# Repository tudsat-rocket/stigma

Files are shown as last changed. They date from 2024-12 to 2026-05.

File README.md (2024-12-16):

# Stigma

the core- and mission board for our new flight computer

## Core Board
The core board will be placed on the mission board and will contain all basic and always-needed stuff. Powered by an STM32H7

## Mission Board
The mission board will contain all the other components but may change for future use cases of the core board.

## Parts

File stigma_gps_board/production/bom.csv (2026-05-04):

Designator | Footprint | Quantity | Value | LCSC Part #
C1, C2 | 0603 | 2 | 1uF | C15849
C3, C4, C5 | 0603 | 3 | 100n | C14663
J1 | DF40GB-70DP-0.4V-plug | 1 | DF40GB-70DP-0.4V | C2692097
L1 | 0603 | 1 | BEAD | C19330
L2 | 0603 | 1 | BEAD
TP1 | TestPoint_Pad_D1.5mm | 1 | tx
TP2 | TestPoint_Pad_D1.5mm | 1 | rx
TP3 | TestPoint_Pad_D1.5mm | 1 | 3v3
U1 | TSOP-5_1.65x3.05mm_P0.95mm | 1 | NCP115AMX120TCG | C603505

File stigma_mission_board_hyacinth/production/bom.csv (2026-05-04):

Designator | Footprint | Quantity | Value | LCSC Part #
BZ1 | MagneticBuzzer_CUI_CMT-8504-100-SMT | 1 | Buzzer | C781886
C10, C16, C18, C22, C23, C3, C8 | 0805 | 7 | 22u | C45783
C11, C14, C25, C26, C27, C28, C29, C30, C35, C36, C37, C38, C39, C40, C44, C45, C49, C57 | 0402 | 18 | 100n | C1525
C15, C17, C21, C34, C4, C43, C48, C7, C9 | 0603 | 9 | 10u | C96446
C19, C20, C41, C5 | 0402 | 4 | 1u | C52923
C24, C6 | 0603 | 2 | 10u
C42 | 0402 | 1 | 470p | C1537
C50, C51 | 0402 | 2 | 10p | C32949
C52, C54 | 0402 | 2 | 100n
C53 | 0402 | 1 | 33n | C7419416
C55, C56 | 0603 | 2 | 22u | C45783
D10, D16, D17, D18, D19 | 0603 | 5 | white | C2290
D15, D2, D3 | D_SMA | 3 | SS34 | C8678
D5, D6, D8 | 0603 | 3 | red | C2286
F1 | 1206 | 1 | 3A | C99558
F2, F3, F4, F5 | 1206 | 4 | 10A | C207003
FB1 | 0603 | 1 | FerriteBead | C1002
J1, J2 | core-board-inner-mounting-holes | 2 | DF40C-70DS-0.4V(51) | C294854
J10, J9 | JST_GH_SM04B-GHS-TB_1x04-1MP_P1.25mm_Horizontal | 2 | JST-GH | C189895
J3, J4 | Molex_Micro-Fit_3.0_43045-0800_2x04_P3.00mm_Horizontal | 2 | ~
J5 | Molex_Micro-Fit_3.0_43045-1200_2x06_P3.00mm_Horizontal | 1 | ~
J6, J7 | SMA_Amphenol_132289_EdgeMount | 2 | SMA
J8 | RJ45_Wuerth_7499010211A_Horizontal | 1 | RJ45_Wuerth_7499010211A
JP3, JP4 | PinHeader_1x02_P1.27mm_Vertical | 2 | Jumper_2_Small_Open
JP5 | SolderJumper-2_P1.3mm_Bridged_Pad1.0x1.5mm | 1 | Jumper_2_Bridged
L1 | L_Wuerth_XHMI-6060 | 1 | 6u8
Q1 | DFN-8-1EP_3x3mm_P0.65mm_EP1.55x2.4mm | 1 | AON7423 | C99711
Q2, Q4 | SOT-23 | 2 | AO3400A | C20917
Q5, Q6, Q7, Q8 | DFN-8-1EP_3x3mm_P0.65mm_EP1.55x2.4mm | 4 | AON7544 | C315567
R1, R17 | 2512 | 2 | 5m, 1% | C723630
R10, R12, R15, R19, R25, R27, R28, R29, R37, R46, R48, R53, R55, R57, R59, R6, R60, R62, R64, R66, R7, R8, R9 | 0402 | 23 | 10k | C25744
R11, R26 | 0402 | 2 | 1k5 | C25867
R13, R14, R22, R44, R54, R58, R61, R65 | 0402 | 8 | 120 | C25079
R2, R3, R4, R56 | 0402 | 4 | 100k | C25741
R24, R34, R67 | 0603 | 3 | 0
R30, R31, R32, R33 | 0402 | 4 | 51 | C25125
R35, R36, R38, R41, R42, R43, R51, R52 | 0402 | 8 | 33 | C25161
R39, R50 | 0402 | 2 | 0 | C17168
R40 | 0402 | 1 | 12.1k | C25752
R45, R47 | 0603 | 2 | 270 | C22966
R68 | 0402 | 1 | 0
R69 | 0603 | 1 | 56k
R70 | 0603 | 1 | 10k
R72 | 0603 | 1 | 49.9
TP1, TP2, TP3, TP4, TP5, TP6, TP7 | TestPoint_Pad_D1.5mm | 7 | TestPoint
U10, U8 | SOIC-8_3.9x4.9mm_P1.27mm | 2 | MCP2562FD | C124016
U11, U13 | Ai-Thinker-Ra-01-LoRa | 2 | Ai-Thinker-Ra-01
U12 | SOT-563 | 1 | TPD4E1U06 | C527516
U14 | VQFN-24-1EP_4x4mm_P0.5mm_EP2.5x2.5mm_ThermalVias | 1 | LAN8742A | C621424
U15 | SOT-583-8 | 1 | TPS62933
U2, U3, U6, U7 | SOT-223-3_TabPin2 | 4 | AZ1117I-3.3 | C92102
U4 | SOT-23-6 | 1 | INA181A3 | C2652255
U9 | SOT-23-6 | 1 | INA181A2 | C2058784
Y1 | Crystal_SMD_3225-4Pin_3.2x2.5mm | 1 | 25MHz | C9006

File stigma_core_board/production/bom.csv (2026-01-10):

Designator | Footprint | Quantity | Value | LCSC Part #
C1 | 0603 | 1 | 4u7 | C19666
C10, C9 | 0402 | 2 | 2u2 | C12530
C11, C12, C13, C14 | 0402 | 4 | 10p | C32949
C15, C16, C17, C20, C21, C22, C24, C25, C27, C28, C29, C3, C30, C31, C34, C35, C36, C39, C4, C40, C5, C6, C7 | 0402 | 23 | 100n | C1525
C18, C23 | 0603 | 2 | 10u | C19702
C19 | 0603 | 1 | 22u | C86295
C2, C26, C33, C37, C8 | 0402 | 5 | 1u | C52923
C32, C38 | 0402 | 2 | 10n | C15195
D1 | 0603 | 1 | red | C2286
D2 | 0603 | 1 | yellow | C72038
D3 | 0603 | 1 | green | C965804
D4 | D_SOD-123 | 1 | ~ | C8598
FB1 | 0603 | 1 | FerriteBead_Small | C1002
J1 | Tag-Connect_TC2050-IDC-FP_2x05_P1.27mm_Vertical | 1 | TC2050
J3 | DF40GB-70DP-0.4V-plug | 1 | CONN PLUG 70POS SMD GOLD
J5 | USB_C_Receptacle_Palconn_UTC16-G | 1 | USB_C_Receptacle_USB2.0 | C709357
R1, R2, R3, R4 | 0402 | 4 | 0 | C17168
R10, R11 | 0402 | 2 | 5k1 | C25905
R12, R13, R16, R17, R18, R19, R20 | 0402 | 7 | 22 | C25092
R14 | 0402 | 1 | 4k7 | C25900
R15 | 0402 | 1 | 10k | C25744
R5 | 0402 | 1 | 100k | C25741
R6, R7, R8, R9 | 0402 | 4 | 1k | C11702
SW1, SW2 | SW_Push_1P1T_NO_CK_KMR2 | 2 | KMR721NGLFS | C2911418
U1 | LQFP-100_14x14mm_P0.5mm | 1 | STM32H743VIT6 | C114409
U10 | LGA-16_3x3mm_P0.5mm_LayoutBorder3x5y | 1 | H3LIS331DL | C2655074
U11 | LGA-8_3x5mm_P1.25mm | 1 | MS5607/MS5611 | C97627
U12 | LGA-12_2x2mm_P0.5mm | 1 | LIS3MDL | C478483
U13 | ST_HLGA-10_2x2mm_P0.5mm_LayoutBorder3x2y | 1 | BMP580 | C22391138
U2, U7 | SOT-563 | 2 | TPD4E1U06 | C527516
U3 | ST_HLGA-10_2x2mm_P0.5mm_LayoutBorder3x2y | 1 | LPS22 | C2827824
U4 | LGA-14_3x2.5mm_P0.5mm_LayoutBorder3x4y | 1 | ICM-42670-P | C3288646
U5 | SOT-223-3_TabPin2 | 1 | AZ1117I-3.3 | C92102
U6 | LGA-14_3x2.5mm_P0.5mm_LayoutBorder3x4y | 1 | ICM-42688-P | C1850418
U8 | WSON-8-1EP_8x6mm_P1.27mm_EP3.4x4.3mm | 1 | W25Q256JVEIQ | C97522
U9 | LGA-14_3x2.5mm_P0.5mm_LayoutBorder3x4y | 1 | LSM6DSR | C784817
Y1 | Crystal_SMD_3225-4Pin_3.2x2.5mm | 1 | 25MHz | C9006
Y2 | Crystal_SMD_3215-2Pin_3.2x1.5mm | 1 | 32.768kHz | C70509

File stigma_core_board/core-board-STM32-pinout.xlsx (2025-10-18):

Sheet: H743xIG Pins
# | Name/Function | AF (Core Board) | Conn. Pin | AF (Mission Board Opt. 1) | AF (Mission Board Opt. 2) | ADC | Use/Notes | Timers | USB (OTG) | UART | DAC | Other | Additional functions | Alternate functions | https://www.st.com/resource/en/datasheet/stm32h743bi.pdf
94 | BOOT0 |  |  |  |  |  |  |  |  |  |  |  | VPP
14 | NRST
22 | PA0 |  | 59 |  | UART4_TX | 1_INP16 |  | 2_CH1 2_ETR 5_CH1 8_ETR |  | 4_TX |  | USART2_CTS/USART2_NSS SDMMC2_CMD | ADC1_INP16,WKUP1 | TIM2_CH1/TIM2_ETR,TIM5_CH1, TIM8_ETR,TIM15_BKIN,USART2_CTS/USART2_NSS, UART4_TX,SDMMC2_CMD,SAI2_SD_B,ETH_MII_CRS,EVENTOUT
23 | PA1 |  | 60 | ETH_RMII_REF_CLK | UART4_RX | 1_INN16 1_INP17 |  | 2_CH2 5_CH2 3_OUT |  | 4_RX |  | LP USART2_RTS/USART2_DE LCD_R2 | ADC1_INN16,ADC1_INP17 | TIM2_CH2, TIM5_CH2,LPTIM3_OUT,TIM15_CH1N,USART2_RTS/USART2_DE, UART4_RX,QUADSPI_BK1_IO3,SAI2_MCLK_B,ETH_MII_RX_CLK/ETH_RMII_REF_CLK,LCD_R2, EVENTOUT
69 | PA10 | Output/Timer |  |  |  |  | LED | 1_CH3 | FS_ID | 1_RX 1_RX |  | HRTIM_CHC2 LP USART1_RX MDIOS_MDIO LCD_B4 DCMI_D1 LCD_B1 |  | TIM1_CH3,HRTIM_CHC2,LPUART1_RX,USART1_RX,OTG_FS_ID,MDIOS_MDIO, LCD_B4,DCMI_D1, LCD_B1,EVENTOUT
70 | PA11 | OTG_FS_DM |  |  |  |  |  | 1_CH4 | FS_DM | 4_RX |  | HRTIM_CHD1 LP USART1_CTS/USART1_NSS LCD_R4 |  | TIM1_CH4,HRTIM_CHD1,LPUART1_CTS,SPI2_NSS/I2S2_WS,UART4_RX,USART1_CTS/USART1_NSS, FDCAN1_RX,OTG_FS_DM, LCD_R4,EVENTOUT
71 | PA12 | OTG_FS_DP |  |  |  |  |  | 1_ETR | FS_DP | 4_TX |  | HRTIM_CHD2 LP USART1_RTS/USART1_DE LCD_R5 |  | TIM1_ETR,HRTIM_CHD2,LPUART1_RTS/LPUART1_DE,SPI2_SCK/I2S2_CK,UART4_TX,USART1_RTS/USART1_DE, SAI2_FS_B,FDCAN1_TX,OTG_FS_DP, LCD_R5,EVENTOUT
72 | PA13(JTMS/SWDIO) |  |  |  |  |  |  |  |  |  |  | JTMS-SWDIO |  | JTMS-SWDIO,EVENTOUT
76 | PA14(JTCK/SWCLK) |  |  |  |  |  |  |  |  |  |  | JTCK-SWCLK |  | JTCK-SWCLK,EVENTOUT
77 | PA15(JTDI) | Output/Timer |  |  |  |  | LED | 2_CH1 2_ETR |  | 7_TX |  | JTDI HRTIM_FLT1 CEC |  | JTDI,TIM2_CH1/TIM2_ETR,HRTIM_FLT1, CEC,SPI1_NSS/I2S1_WS,SPI3_NSS/I2S3_WS,SPI6_NSS,UART4_RTS/UART4_DE, UART7_TX,EVENTOUT
24 | PA2 |  | 61 | ETH_MDIO | UART2_TX | 12_INP14 |  | 2_CH3 5_CH3 4_OUT |  | 2_TX |  | LP USART2_TX MDIOS_MDIO LCD_R1 | ADC12_INP14,WKUP2 | TIM2_CH3, TIM5_CH3,LPTIM4_OUT,TIM15_CH1,USART2_TX,SAI2_SCK_B,ETH_MDIO,MDIOS_MDIO, LCD_R1,EVENTOUT
25 | PA3 |  | 62 | ADC12_INP15 | UART2_RX | 12_INP15 |  | 2_CH4 5_CH4 5_OUT | HS_ULPI_D0 | 2_RX |  | LP USART2_RX LCD_B2 LCD_B5 | ADC12_INP15 | TIM2_CH4, TIM5_CH4,LPTIM5_OUT,TIM15_CH2,USART2_RX, LCD_B2,OTG_HS_ULPI_D0,ETH_MII_COL, LCD_B5,EVENTOUT
28 | PA4 |  | 64 | ADC12_INP18 | DAC1_OUT1 | 12_INP18 |  | 5_ETR | HS_SOF |  | 1_OUT1 | D1PWREN USART2_CK DCMI_HSYNC LCD_VSYNC | ADC12_INP18,DAC1_OUT1 | D1PWREN, TIM5_ETR,SPI1_NSS/I2S1_WS,SPI3_NSS/I2S3_WS,USART2_CK, SPI6_NSS,OTG_HS_SOF,DCMI_HSYNC,LCD_VSYNC,EVENTOUT
29 | PA5 | SPI1_SCK |  |  |  | 12_INN18 12_INP19 |  | 2_CH1 2_ETR 8_CH1N | HS_ULPI_CK |  | 1_OUT2 | D2PWREN LCD_R4 | ADC12_INN18,ADC12_INP19,DAC1_OUT2 | D2PWREN,TIM2_CH1/TIM2_ETR,TIM8_CH1N,SPI1_SCK/I2S1_CK,SPI6_SCK,OTG_HS_ULPI_CK,LCD_R4, EVENTOUT
30 | PA6 |  | 65 |  |  | 12_INP3 |  | 1_BKIN 3_CH1 8_BKIN 8_BKIN_COMP12 1_BKIN_COMP12 |  |  |  | MDIOS_MDC DCMI_PIXCLK LCD_G2 | ADC12_INP3 | TIM1_BKIN, TIM3_CH1,TIM8_BKIN,SPI1_MISO/I2S1_SDI,SPI6_MISO, TIM13_CH1,TIM8_BKIN_COMP12,MDIOS_MDC,TIM1_BKIN_COMP12,DCMI_PIXCLK, LCD_G2,EVENTOUT
31 | PA7 |  | 66 | ETH_RMII_CRS_DV |  | 12_INN3 12_INP7 |  | 1_CH1N 3_CH2 8_CH1N |  |  |  |  | ADC12_INN3,ADC12_INP7,OPAMP1_VINM | TIM1_CH1N, TIM3_CH2,TIM8_CH1N,SPI1_MOSI/I2S1_SDO,SPI6_MOSI, TIM14_CH1,ETH_MII_RX_DV/ETH_RMII_CRS_DV,FMC_SDNWE,EVENTOUT
67 | PA8 | Output/Timer |  |  |  |  | LED | 1_CH1 8_BKIN2 8_BKIN2_COMP12 | FS_SOF | 7_RX |  | MCO1 HRTIM_CHB2 I2C3_SCL USART1_CK LCD_B3 LCD_R6 |  | MCO1, TIM1_CH1,HRTIM_CHB2,TIM8_BKIN2, I2C3_SCL,USART1_CK,OTG_FS_SOF,UART7_RX,TIM8_BKIN2_COMP12,LCD_B3, LCD_R6,EVENTOUT
68 | PA9 | USB VBUS detection |  |  |  |  |  | 1_CH2 |  | 1_TX 1_TX |  | HRTIM_CHC1 LP I2C3_SMBA USART1_TX DCMI_D0 LCD_R5 | OTG_FS_VBUS | TIM1_CH2,HRTIM_CHC1,LPUART1_TX,I2C3_SMBA,SPI2_SCK/I2S2_CK,USART1_TX, DCMI_D0,LCD_R5, EVENTOUT
34 | PB0 |  | 46 |  |  | 12_INN5 12_INP9 |  | 1_CH2N 3_CH3 8_CH2N | HS_ULPI_D1 |  |  | LCD_R3 LCD_G1 | ADC12_INN5,ADC12_INP9,OPAMP1_VINP,COMP1_INP | TIM1_CH2N, TIM3_CH3,TIM8_CH2N,DFSDM1_CKOUT,UART4_CTS, LCD_R3,OTG_HS_ULPI_D1,ETH_MII_RXD2,LCD_G1, EVENTOUT
35 | PB1 |  | 47 |  |  | 12_INP5 |  | 1_CH3N 3_CH4 8_CH3N | HS_ULPI_D2 |  |  | LCD_R6 LCD_G0 | ADC12_INP5,COMP1_INM | TIM1_CH3N, TIM3_CH4,TIM8_CH3N,DFSDM1_DATIN1,LCD_R6,OTG_HS_ULPI_D2,ETH_MII_RXD3,LCD_G0, EVENTOUT
46 | PB10 |  | 54 |  | TIM2_CH3 |  |  | 2_CH3 2_IN1 | HS_ULPI_D3 | 3_TX |  | HRTIM_SCOUT LP I2C2_SCL USART3_TX LCD_G4 |  | TIM2_CH3,HRTIM_SCOUT,LPTIM2_IN1, I2C2_SCL,SPI2_SCK/I2S2_CK,DFSDM1_DATIN7,USART3_TX,QUADSPI_BK1_NCS,OTG_HS_ULPI_D3,ETH_MII_RX_ER,LCD_G4, EVENTOUT
47 | PB11 |  | 55 | ETH_RMII_TX_EN | TIM2_CH4 |  |  | 2_CH4 2_ETR | HS_ULPI_D4 | 3_RX |  | HRTIM_SCIN LP I2C2_SDA USART3_RX LCD_G5 |  | TIM2_CH4,HRTIM_SCIN,LPTIM2_ETR,I2C2_SDA,DFSDM1_CKIN7,USART3_RX,OTG_HS_ULPI_D4,ETH_MII_TX_EN/ETH_RMII_TX_EN, LCD_G5,EVENTOUT
51 | PB12 |  | 56 | ETH_RMII_TXD0 | FDCAN2_RX |  |  | 1_BKIN 1_BKIN_COMP12 | HS_ULPI_D5 HS_ID | 5_RX |  | I2C2_SMBA USART3_CK |  | TIM1_BKIN, I2C2_SMBA,SPI2_NSS/I2S2_WS,DFSDM1_DATIN1,USART3_CK,FDCAN2_RX,OTG_HS_ULPI_D5,ETH_MII_TXD0/ETH_RMII_TXD0, OTG_HS_ID,TIM1_BKIN_COMP12,UART5_RX, EVENTOUT
52 | PB13 |  | 57 | ETH_RMII_TXD1 | FDCAN2_TX |  |  | 1_CH1N 2_OUT | HS_ULPI_D6 | 5_TX |  | LP USART3_CTS/USART3_NSS | OTG_HS_VBUS | TIM1_CH1N,LPTIM2_OUT,SPI2_SCK/I2S2_CK,DFSDM1_CKIN1,USART3_CTS/USART3_NSS, FDCAN2_TX,OTG_HS_ULPI_D6,ETH_MII_TXD1/ETH_RMII_TXD1, UART5_TX,EVENTOUT
53 | PB14 | SPI2_MISO |  |  |  |  |  | 1_CH2N 8_CH2N | HS_DM | 1_TX |  | USART1_TX USART3_RTS/USART3_DE SDMMC2_D0 |  | TIM1_CH2N,TIM12_CH1,TIM8_CH2N,USART1_TX,SPI2_MISO/I2S2_SDI,DFSDM1_DATIN2,USART3_RTS/USART3_DE,UART4_RTS/UART4_DE, SDMMC2_D0,OTG_HS_DM,EVENTOUT
54 | PB15 | SPI2_MOSI |  |  |  |  |  | 1_CH3N 8_CH3N | HS_DP | 1_RX |  | RTC_REFIN USART1_RX SDMMC2_D1 |  | RTC_REFIN,TIM1_CH3N,TIM12_CH2,TIM8_CH3N,USART1_RX,SPI2_MOSI/I2S2_SDO,DFSDM1_CKIN2,UART4_CTS,SDMMC2_D1,OTG_HS_DP,EVENTOUT
36 | PB2 |  |  |  |  |  |  |  |  |  |  | RTC_OUT | COMP1_INP | RTC_OUT, SAI1_D1,DFSDM1_CKIN1,SAI1_SD_A,SPI3_MOSI/I2S3_SDO,SAI4_SD_A,QUADSPI_CLK,SAI4_D1, EVENTOUT
89 | PB3(JTDO/TRACESWO) | SWO |  |  |  |  |  | 2_CH2 |  | 7_RX |  | JTDO/TRACESWO HRTIM_FLT4 SDMMC2_D2 CRS_SYNC |  | JTDO/TRACESWO,TIM2_CH2,HRTIM_FLT4,SPI1_SCK/I2S1_CK,SPI3_SCK/I2S3_CK,SPI6_SCK,SDMMC2_D2,CRS_SYNC, UART7_RX,EVENTOUT
90 | PB4(NJTRST) | SPI1_MISO |  |  |  |  |  | 3_CH1 |  | 7_TX |  | NJTRST HRTIM_EEV6 SDMMC2_D3 |  | NJTRST, TIM16_BKIN,TIM3_CH1,HRTIM_EEV6,SPI1_MISO/I2S1_SDI,SPI3_MISO/I2S3_SDI,SPI2_NSS/I2S2_WS,SPI6_MISO,SDMMC2_D3,UART7_TX, EVENTOUT
91 | PB5 |  | 13 | FDCAN2_RX | UART5_RX |  |  | 3_CH2 | HS_ULPI_D7 | 5_RX |  | HRTIM_EEV7 I2C1_SMBA I2C4_SMBA DCMI_D10 |  | TIM17_BKIN, TIM3_CH2,HRTIM_EEV7,I2C1_SMBA,SPI1_MOSI/I2S1_SDO,I2C4_SMBA,SPI3_MOSI/I2S3_SDO,SPI6_MOSI,FDCAN2_RX,OTG_HS_ULPI_D7,ETH_PPS_OUT,FMC_SDCKE1,DCMI_D10, UART5_RX,EVENTOUT
92 | PB6 |  | 14 | FDCAN2_TX | UART5_TX |  |  | 4_CH1 |  | 1_TX 1_TX 5_TX |  | HRTIM_EEV8 I2C1_SCL CEC I2C4_SCL USART1_TX LP DCMI_D5 |  | TIM16_CH1N,TIM4_CH1,HRTIM_EEV8,I2C1_SCL, CEC,I2C4_SCL, USART1_TX,LPUART1_TX,FDCAN2_TX,QUADSPI_BK1_NCS,DFSDM1_DATIN5,FMC_SDNE1, DCMI_D5,UART5_TX, EVENTOUT
93 | PB7 |  | 15 |  |  |  |  | 4_CH2 |  | 1_RX 1_RX |  | HRTIM_EEV9 I2C1_SDA I2C4_SDA USART1_RX LP DCMI_VSYNC | PVD_IN | TIM17_CH1N,TIM4_CH2,HRTIM_EEV9,I2C1_SDA, I2C4_SDA,USART1_RX,LPUART1_RX,DFSDM1_CKIN5,FMC_NL, DCMI_VSYNC,EVENTOUT
95 | PB8 |  | 16 | FDCAN1_RX |  |  |  | 4_CH3 |  | 4_RX |  | I2C1_SCL I2C4_SCL SDMMC1_CKIN SDMMC2_D4 SDMMC1_D4 DCMI_D6 LCD_B6 |  | TIM16_CH1, TIM4_CH3,DFSDM1_CKIN7,I2C1_SCL, I2C4_SCL,SDMMC1_CKIN,UART4_RX,FDCAN1_RX,SDMMC2_D4,ETH_MII_TXD3,SDMMC1_D4, DCMI_D6,LCD_B6, EVENTOUT
96 | PB9 |  | 17 | FDCAN1_TX |  |  |  | 4_CH4 |  | 4_TX |  | I2C1_SDA I2C4_SDA SDMMC1_CDIR SDMMC2_D5 I2C4_SMBA SDMMC1_D5 DCMI_D7 LCD_B7 |  | TIM17_CH1, TIM4_CH4,DFSDM1_DATIN7,I2C1_SDA,SPI2_NSS/I2S2_WS,I2C4_SDA,SDMMC1_CDIR,UART4_TX,FDCAN1_TX,SDMMC2_D5,I2C4_SMBA,SDMMC1_D5, DCMI_D7,LCD_B7, EVENTOUT
15 | PC0 |  | 67 |  |  | 123_INP10 |  |  | HS_ULPI_STP |  |  | LCD_R5 | ADC123_INP10 | DFSDM1_CKIN0,DFSDM1_DATIN4,SAI2_FS_B,OTG_HS_ULPI_STP,FMC_SDNWE, LCD_R5,EVENTOUT
16 | PC1 |  | 27 | ETH_MDC |  | 123_INN10 123_INP11 |  |  |  |  |  | SDMMC2_CK MDIOS_MDC | ADC123_INN10,ADC123_INP11,RTC_TAMP3/WKUP6 | TRACED0, SAI1_D1,DFSDM1_DATIN0,DFSDM1_CKIN4,SPI2_MOSI/I2S2_SDO,SAI1_SD_A, SAI4_SD_A,SDMMC2_CK, SAI4_D1,ETH_MDC,MDIOS_MDC,EVENTOUT
78 | PC10 | SPI3_SCK | 23 | ~~SPI3_SCK~~ | ~~UART4_TX~~ |  |  |  |  | 3_TX 4_TX |  | HRTIM_EEV1 USART3_TX SDMMC1_D2 DCMI_D8 LCD_R2 |  | HRTIM_EEV1,DFSDM1_CKIN5,SPI3_SCK/I2S3_CK,USART3_TX,UART4_TX,QUADSPI_BK1_IO1,SDMMC1_D2, DCMI_D8,LCD_R2, EVENTOUT
79 | PC11 | SPI3_MISO | 24 | ~~SPI3_MISO~~ | ~~UART4_RX~~ |  |  |  |  | 3_RX 4_RX |  | HRTIM_FLT2 USART3_RX SDMMC1_D3 DCMI_D4 |  | HRTIM_FLT2,DFSDM1_DATIN5,SPI3_MISO/I2S3_SDI,USART3_RX,UART4_RX,QUADSPI_BK2_NCS,SDMMC1_D3, DCMI_D4,EVENTOUT
80 | PC12 | SPI3_MOSI | 25 | ~~SPI3_MOSI~~ |  |  |  |  |  | 5_TX |  | HRTIM_EEV2 USART3_CK SDMMC1_CK DCMI_D9 |  | TRACED3,HRTIM_EEV2,SPI3_MOSI/I2S3_SDO,USART3_CK,UART5_TX,SDMMC1_CK, DCMI_D9,EVENTOUT
7 | PC13 | Output |  |  |  |  | CS for Flash |  |  |  |  |  | RTC_TAMP1/RTC_TS/WKUP4 | EVENTOUT
8 | PC14-OSC32_IN |  |  |  |  |  |  |  |  |  |  |  | OSC32_IN | EVENTOUT
9 | PC15-OSC32_OUT |  |  |  |  |  |  |  |  |  |  |  | OSC32_OUT | EVENTOUT
17 | PC2_C |  | 28 |  |  | 3_INN1 3_INP0 |  |  | HS_ULPI_DIR |  |  | CDSLEEP | ADC3_INN1,ADC3_INP0 | CDSLEEP,DFSDM1_CKIN1,SPI2_MISO/I2S2_SDI,DFSDM1_CKOUT,OTG_HS_ULPI_DIR,ETH_MII_TXD2,FMC_SDNE0,EVENTOUT
18 | PC3_C |  | 29 |  |  | 3_INP1 |  |  | HS_ULPI_NXT |  |  | CSLEEP | ADC3_INP1 | CSLEEP,DFSDM1_DATIN1,SPI2_MOSI/I2S2_SDO,OTG_HS_ULPI_NXT,ETH_MII_TX_CLK,FMC_SDCKE0,EVENTOUT
32 | PC4 |  | 31 | ETH_RMII_RXD0 |  | 12_INP4 |  |  |  |  |  | I2S1_MCK SPDIFRX1_IN3 | ADC12_INP4,OPAMP1_VOUT,COMP1_INM | DFSDM1_CKIN2,I2S1_MCK,SPDIFRX1_IN3,ETH_MII_RXD0/ETH_RMII_RXD0, FMC_SDNE0,EVENTOUT
33 | PC5 |  | 32 | ETH_RMII_RXD1 |  | 12_INN4 12_INP8 |  |  |  |  |  | SPDIFRX1_IN4 COMP1_OUT | ADC12_INN4,ADC12_INP8,OPAMP1_VINM | SAI1_D3,DFSDM1_DATIN2,SPDIFRX1_IN4,SAI4_D3,ETH_MII_RXD1/ETH_RMII_RXD1,FMC_SDCKE0,COMP1_OUT,EVENTOUT
63 | PC6 |  | 19 | UART6_TX | TIM3_CH1 |  |  | 3_CH1 8_CH1 |  | 6_TX |  | HRTIM_CHA1 I2S2_MCK USART6_TX SDMMC1_D0DIR SDMMC2_D6 SDMMC1_D6 DCMI_D0 LCD_HSYNC | SWPMI_IO | HRTIM_CHA1,TIM3_CH1, TIM8_CH1,DFSDM1_CKIN3,I2S2_MCK, USART6_TX,SDMMC1_D0DIR,FMC_NWAIT,SDMMC2_D6,SDMMC1_D6, DCMI_D0,LCD_HSYNC,EVENTOUT
64 | PC7 |  | 20 | UART6_RX | TIM3_CH2 |  |  | 3_CH2 8_CH2 |  | 6_RX |  | TRGIO HRTIM_CHA2 I2S3_MCK USART6_RX SDMMC1_D123DIR SDMMC2_D7 SWPMI_TX SDMMC1_D7 DCMI_D1 LCD_G6 |  | TRGIO, HRTIM_CHA2,TIM3_CH2, TIM8_CH2,DFSDM1_DATIN3,I2S3_MCK,USART6_RX,SDMMC1_D123DIR,FMC_NE1,SDMMC2_D7,SWPMI_TX,SDMMC1_D7, DCMI_D1,LCD_G6, EVENTOUT
65 | PC8 |  | 21 |  | TIM3_CH3 |  |  | 3_CH3 8_CH3 |  |  |  | HRTIM_CHB1 USART6_CK SWPMI_RX SDMMC1_D0 DCMI_D2 |  | TRACED1,HRTIM_CHB1,TIM3_CH3, TIM8_CH3,USART6_CK,UART5_RTS/UART5_DE, FMC_NE2/FMC_NCE,SWPMI_RX,SDMMC1_D0, DCMI_D2,EVENTOUT
66 | PC9 |  | 22 |  | TIM3_CH4 |  |  | 3_CH4 8_CH4 |  |  |  | MCO2 I2C3_SDA I2S_CKIN LCD_G3 SWPMI_SUSPEND SDMMC1_D1 DCMI_D3 LCD_B2 |  | MCO2, TIM3_CH4,TIM8_CH4, I2C3_SDA,I2S_CKIN, UART5_CTS,QUADSPI_BK1_IO0,LCD_G3,SWPMI_SUSPEND,SDMMC1_D1, DCMI_D3,LCD_B2, EVENTOUT
81 | PD0 |  | 4 | UART4_RX |  |  |  |  |  | 4_RX |  |  |  | DFSDM1_CKIN6,SAI3_SCK_A,UART4_RX,FDCAN1_RX,FMC_D2/FMC_DA2,EVENTOUT
82 | PD1 |  | 5 | UART4_TX |  |  |  |  |  | 4_TX |  |  |  | DFSDM1_DATIN6,SAI3_SD_A, UART4_TX,FDCAN1_TX,FMC_D3/FMC_DA3,EVENTOUT
57 | PD10 |  |  |  |  |  |  |  |  |  |  | USART3_CK LCD_B3 |  | DFSDM1_CKOUT,SAI3_FS_B,USART3_CK,FMC_D15/FMC_DA15,LCD_B3, EVENTOUT
58 | PD11 |  |  |  |  |  |  | 2_IN2 |  |  |  | LP I2C4_SMBA USART3_CTS/USART3_NSS |  | LPTIM2_IN2,I2C4_SMBA,USART3_CTS/USART3_NSS,QUADSPI_BK1_IO0,SAI2_SD_A, FMC_A16,EVENTOUT
59 | PD12 |  | 6 |  |  |  |  | 1_IN1 4_CH1 2_IN1 |  |  |  | LP LP I2C4_SCL USART3_RTS/USART3_DE |  | LPTIM1_IN1, TIM4_CH1,LPTIM2_IN1, I2C4_SCL,USART3_RTS/USART3_DE, QUADSPI_BK1_IO1,SAI2_FS_A, FMC_A17,EVENTOUT
60 | PD13 |  | 7 |  |  |  |  | 1_OUT 4_CH2 |  |  |  | LP I2C4_SDA |  | LPTIM1_OUT,TIM4_CH2, I2C4_SDA,QUADSPI_BK1_IO3,SAI2_SCK_A, FMC_A18,EVENTOUT
61 | PD14 |  | 8 |  |  |  |  | 4_CH3 |  |  |  |  |  | TIM4_CH3,SAI3_MCLK_B,UART8_CTS,FMC_D0/FMC_DA0,EVENTOUT
62 | PD15 |  | 9 |  |  |  |  | 4_CH4 |  |  |  |  |  | TIM4_CH4,SAI3_MCLK_A,UART8_RTS/UART8_DE, FMC_D1/FMC_DA1,EVENTOUT
83 | PD2 | Output |  |  |  |  | CS for Mag | 3_ETR |  | 5_RX |  | SDMMC1_CMD DCMI_D11 |  | TRACED2, TIM3_ETR,UART5_RX,SDMMC1_CMD,DCMI_D11, EVENTOUT
84 | PD3 | SPI2_SCK |  |  |  |  |  |  |  |  |  | USART2_CTS/USART2_NSS DCMI_D5 LCD_G7 |  | DFSDM1_CKOUT,SPI2_SCK/I2S2_CK,USART2_CTS/USART2_NSS, FMC_CLK,DCMI_D5, LCD_G7,EVENTOUT
85 | PD4 | Output |  |  |  |  | CS for IMU1 |  |  |  |  | HRTIM_FLT3 USART2_RTS/USART2_DE |  | HRTIM_FLT3,SAI3_FS_A,USART2_RTS/USART2_DE, FMC_NOE,EVENTOUT
86 | PD5 | Output |  |  |  |  | CS for IMU2 |  |  | 2_TX |  | HRTIM_EEV3 USART2_TX |  | HRTIM_EEV3,USART2_TX,FMC_NWE, EVENTOUT
87 | PD6 | Output |  |  |  |  | CS for IMU3 |  |  | 2_RX |  | USART2_RX SDMMC2_CK DCMI_D10 LCD_B2 |  | SAI1_D1,DFSDM1_CKIN4,DFSDM1_DATIN1,SPI3_MOSI/I2S3_SDO,SAI1_SD_A,USART2_RX,SAI4_SD_A, SAI4_D1,SDMMC2_CK,FMC_NWAIT,DCMI_D10, LCD_B2,EVENTOUT
88 | PD7 | SPI1_MOSI |  |  |  |  |  |  |  |  |  | USART2_CK SPDIFRX1_IN1 SDMMC2_CMD |  | DFSDM1_DATIN4,SPI1_MOSI/I2S1_SDO,DFSDM1_CKIN1,USART2_CK,SPDIFRX1_IN1,SDMMC2_CMD,FMC_NE1, EVENTOUT
55 | PD8 | Output |  |  |  |  | CS for Acc. |  |  | 3_TX |  | USART3_TX SPDIFRX1_IN2 |  | DFSDM1_CKIN3,SAI3_SCK_B,USART3_TX,SPDIFRX1_IN2,FMC_D13/FMC_DA13,EVENTOUT
56 | PD9 | Output |  |  |  |  | CS for Baro1 |  |  | 3_RX |  | USART3_RX |  | DFSDM1_DATIN3,SAI3_SD_B,USART3_RX,FMC_D14/FMC_DA14,EVENTOUT
97 | PE0 |  | 4 | UART8_RX |  |  |  | 1_ETR 4_ETR 2_ETR |  | 8_RX |  | LP HRTIM_SCIN LP DCMI_D2 |  | LPTIM1_ETR,TIM4_ETR,HRTIM_SCIN,LPTIM2_ETR,UART8_RX,SAI2_MCLK_A,FMC_NBL0, DCMI_D2,EVENTOUT
98 | PE1 |  | 5 | UART8_TX |  |  |  | 1_IN2 |  | 8_TX |  | LP HRTIM_SCOUT DCMI_D3 |  | LPTIM1_IN2,HRTIM_SCOUT,UART8_TX, FMC_NBL1,DCMI_D3, EVENTOUT
40 | PE10 |  | 13 | TIM1_CH2N |  |  |  | 1_CH2N |  |  |  |  | COMP2_INM | TIM1_CH2N,DFSDM1_DATIN4,UART7_CTS,QUADSPI_BK2_IO3,FMC_D7/FMC_DA7,EVENTOUT
41 | PE11 |  | 14 | TIM1_CH2 |  |  |  | 1_CH2 |  |  |  | LCD_G3 | COMP2_INP | TIM1_CH2,DFSDM1_CKIN4,SPI4_NSS, SAI2_SD_B,FMC_D8/FMC_DA8,LCD_G3, EVENTOUT
42 | PE12 |  | 15 | TIM1_CH3N | SPI4_SCK |  |  | 1_CH3N |  |  |  | COMP1_OUT LCD_B4 |  | TIM1_CH3N,DFSDM1_DATIN5,SPI4_SCK,SAI2_SCK_B,FMC_D9/FMC_DA9,COMP1_OUT, LCD_B4,EVENTOUT
43 | PE13 |  | 16 | TIM1_CH3 | SPI4_MISO |  |  | 1_CH3 |  |  |  | COMP2_OUT LCD_DE |  | TIM1_CH3,DFSDM1_CKIN5,SPI4_MISO, SAI2_FS_B,FMC_D10/FMC_DA10,COMP2_OUT, LCD_DE,EVENTOUT
44 | PE14 |  | 17 | TIM1_CH4 | SPI4_MOSI |  |  | 1_CH4 |  |  |  | LCD_CLK |  | TIM1_CH4, SPI4_MOSI,SAI2_MCLK_B,FMC_D11/FMC_DA11,LCD_CLK, EVENTOUT
45 | PE15 |  |  |  |  |  |  | 1_BKIN 1_BKIN_COMP12 1_BKIN |  |  |  | LCD_R7 |  | TIM1_BKIN,FMC_D12/FMC_DA12,TIM1_BKIN_COMP12/COMP_TIM1_BKIN,LCD_R7, EVENTOUT
1 | PE2 |  | 6 | SPI4_SCK |  |  |  |  |  |  |  |  |  | TRACECLK, SAI1_CK1,SPI4_SCK,SAI1_MCLK_A,SAI4_MCLK_A,QUADSPI_BK1_IO2,SAI4_CK1,ETH_MII_TXD3,FMC_A23, EVENTOUT
2 | PE3 | Output |  |  |  |  | CS for Baro2 |  |  |  |  |  |  | TRACED0, TIM15_BKIN,SAI1_SD_B, SAI4_SD_B,FMC_A19, EVENTOUT
3 | PE4 | Output |  |  |  |  | CS for Baro3 |  |  |  |  | DCMI_D4 LCD_B0 |  | TRACED1, SAI1_D2,DFSDM1_DATIN3,TIM15_CH1N,SPI4_NSS, SAI1_FS_A,SAI4_FS_A, SAI4_D2,FMC_A20, DCMI_D4,LCD_B0, EVENTOUT
4 | PE5 |  | 7 | SPI4_MISO |  |  |  |  |  |  |  | DCMI_D6 LCD_G0 |  | TRACED2, SAI1_CK2,DFSDM1_CKIN3,TIM15_CH1, SPI4_MISO,SAI1_SCK_A,SAI4_SCK_A, SAI4_CK2,FMC_A21, DCMI_D6,LCD_G0, EVENTOUT
5 | PE6 |  | 8 | SPI4_MOSI |  |  |  | 1_BKIN2 1_BKIN2_COMP12 |  |  |  | DCMI_D7 LCD_G1 |  | TRACED3, TIM1_BKIN2,SAI1_D1, TIM15_CH2,SPI4_MOSI, SAI1_SD_A,SAI4_SD_A, SAI4_D1,SAI2_MCLK_B,TIM1_BKIN2_COMP12,FMC_A22, DCMI_D7,LCD_G1, EVENTOUT
37 | PE7 |  | 10 |  | UART7_RX |  |  | 1_ETR |  | 7_RX |  |  | OPAMP2_VOUT,COMP2_INM | TIM1_ETR,DFSDM1_DATIN2,UART7_RX,QUADSPI_BK2_IO0,FMC_D4/FMC_DA4,EVENTOUT
38 | PE8 |  | 11 | TIM1_CH1N | UART7_TX |  |  | 1_CH1N |  | 7_TX |  | COMP2_OUT | OPAMP2_VINM | TIM1_CH1N,DFSDM1_CKIN2,UART7_TX,QUADSPI_BK2_IO1,FMC_D5/FMC_DA5,COMP2_OUT,EVENTOUT
39 | PE9 |  | 12 | TIM1_CH1 |  |  |  | 1_CH1 |  |  |  |  | OPAMP2_VINP,COMP2_INP | TIM1_CH1,DFSDM1_CKOUT,UART7_RTS/UART7_DE, QUADSPI_BK2_IO2,FMC_D6/FMC_DA6,EVENTOUT
12 | PH0-OSC_IN |  |  |  |  |  |  |  |  |  |  |  | OSC_IN | EVENTOUT
13 | PH1-OSC_OUT |  |  |  |  |  |  |  |  |  |  |  | OSC_OUT | EVENTOUT
6 | VBAT
48 | VCAP
73 | VCAP
11 | VDD
27 | VDD
50 | VDD
75 | VDD
100 | VDD
21 | VDDA
20 | VREF+
10 | VSS
26 | VSS
49 | VSS
74 | VSS
99 | VSS
19 | VSSA
 |  | USB VBUS detection

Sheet: ConnectorPins
Use on MB |  |  | Comment/Function | Pin | Pin # | Pin # | Pin | Comment/Function |  |  | Use on MB | MB Notes
5V |  |  |  | 5V | 1 | 36 | 5V |  |  |  | 5V
5V |  |  |  | 5V | 2 | 37 | 5V |  |  |  | 5V
GND |  |  |  | GND | 3 | 38 | GND |  |  |  | GND
 |  |  | UART8_RX | PE0 | 4 | 39 | PD0 | UART4_RX |  |  | GPS
 |  |  | UART8_TX | PE1 | 5 | 40 | PD1 | UART4_TX |  |  | GPS
telem. |  |  | SPI4_SCK | PE2 | 6 | 41 | PD12 | TIM4_CH1 |  |  | telem_CS (GPS Reset) | can be subst. with
telem. |  |  | SPI4_MISO | PE5 | 7 | 42 | PD13 | TIM4_CH2 |  |  | telem_CS (GPS Safeboot) | any GPIO output
telem. |  |  | SPI4_MOSI | PE6 | 8 | 43 | PD14 | TIM4_CH3 |  |  | telem_CS (SPI NSS) | depending on routing
GND |  |  |  | GND | 9 | 44 | PD15 | TIM4_CH4 |  |  | telem_CS (SPI Reset) | needs
 |  | UART7_RX |  | PE7 | 10 | 45 | GND |  |  |  | GND
Shift Register |  | UART7_TX | TIM1_CH1N | PE8 | 11 | 46 | PB0 |  |  | ADC12_INN5/INP9 | ADC_REC 2 U
Shift Register |  |  | TIM1_CH1 | PE9 | 12 | 47 | PB1 |  |  | ADC12_INP5 | ADC REC 2 I
Shift Register |  |  | TIM1_CH2N | PE10 | 13 | 48 | PB5 | FDCAN2_RX | UART5_RX |  | CAN
REC 1 cont check |  |  | TIM1_CH2 | PE11 | 14 | 49 | PB6 | FDCAN2_TX | UART5_TX |  | CAN
REC 2 cont check |  |  | TIM1_CH3N | PE12 | 15 | 50 | PB7 | TIM4_CH2 |  |  |  | tie to GND if not used -> add. grounding for can bus
REC 3 cont check |  |  | TIM1_CH3 | PE13 | 16 | 51 | PB8 | FDCAN1_RX |  |  | CAN
Rec 4 cont check |  |  | TIM1_CH4 | PE14 | 17 | 52 | PB9 | FDCAN1_TX |  |  | CAN
GND |  |  |  | GND | 18 | 53 | GND |  |  |  | GND
Recovery |  | UART6_TX | TIM3_CH1 | PC6 | 19 | 54 | PB10 |  | TIM2_CH3 |  | buzzer
Recovery |  | UART6_RX | TIM3_CH2 | PC7 | 20 | 55 | PB11 | ETH_RMII_TX_EN | TIM2_CH4 |  | ethernet
Recovery |  |  | TIM3_CH3 | PC8 | 21 | 56 | PB12 | ETH_RMII_TXD0 |  |  | ethernet
Recovery |  |  | TIM3_CH4 | PC9 | 22 | 57 | PB13 | ETH_RMII_TXD1 |  |  | ethernet
telem. | shared with | ~~UART4_TX~~ | ~~SPI3_SCK~~ | PC10 | 23 | 58 | GND |  |  |  | GND
telem. | core board | ~~UART4_RX~~ | ~~SPI3_MISO~~ | PC11 | 24 | 59 | PA0 |  | UART4_TX | ADC1_INP18 | ADC REC 1 U
telem. | (flash) |  | ~~SPI3_MOSI~~ | PC12 | 25 | 60 | PA1 | ETH_RMII_REF_CLK |  | ADC1_INP17/INN16 | ethernet
gnd |  |  |  | GND | 26 | 61 | PA2 | ETH_MDIO | UART2_TX | ADC12_INP14 | ethernet
ethernet |  | UART4_RX | ETH_MDC | PC1 | 27 | 62 | PA3 |  | UART2_RX | ADC12_INP15 | ADC REC 1 I
ADC high current | ADC3_INN1/INP0 |  |  | PC2_C | 28 | 63 | GND |  |  |  | GND
LoRa nss | ADC3_INP1 |  |  | PC3_C | 29 | 64 | PA4 |  | DAC1_OUT1 | ADC12_INP18 | buzzer?
gnd |  |  |  | GND | 30 | 65 | PA6 |  |  | ADC12_INP3 | ADC_MAIN_VOLTAGE_CURRENT
ethernet |  |  | ETH_RMII_RXD0 | PC4 | 31 | 66 | PA7 | ETH_RMII_CRS_DV |  |  | ethernet
ethernet |  |  | ETH_RMII_RXD1 | PC5 | 32 | 67 | PC0 |  |  | ADC123_INP10 | ADC_MAIN_VOLTAGE
GND |  |  |  | GND | 33 | 68 | GND |  |  |  | GND
5V |  |  |  | 5V | 34 | 69 | 5V |  |  |  | 5V
5V |  |  |  | 5V | 35 | 70 | 5V |  |  |  | 5V
Other useful pins for MB
GPS | reset, (safeboot)
Telem (each). | reset, busy, irq | maybe 2 for each? discuss needs

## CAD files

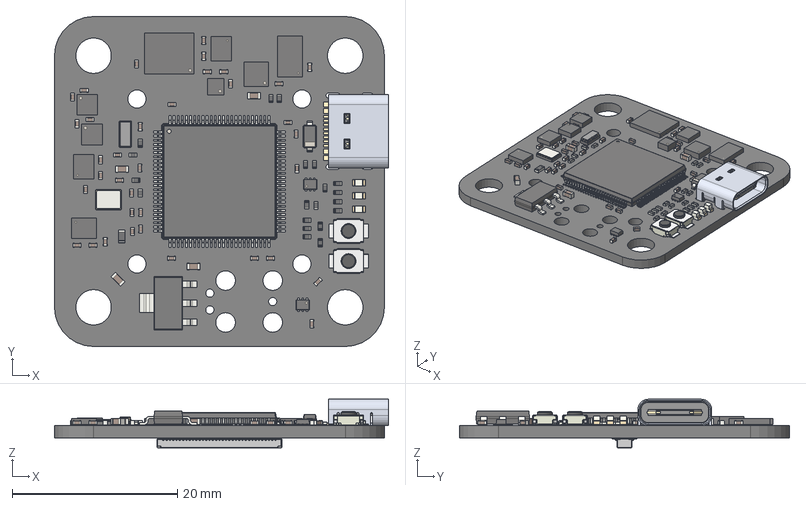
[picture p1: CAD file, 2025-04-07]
stigma_core_board/stigma_core_board.step
40.5 x 40.0 x 5.88 mm
C_0402_1005Metric x 36
LGA-12_2x2mm_P0.5mm
R_0402_1005Metric x 20
SOT-223
LGA-8_3x5mm_P1.25mm
C_0603_1608Metric x 4
LED_0603_1608Metric x 3
usb_c
SW_SPST_B3U-1000P x 2
WSON-8-1EP_6x5mm_P1.27mm_EP3.4x4.3mm
Crystal_SMD_3215-2Pin_3.2x1.5mm
SOT-563 x 2
LGA-14_3x2.5mm_P0.5mm_LayoutBorder3x4y x 3
LGA-16_3x3mm_P0.5mm_LayoutBorder3x5y
ST_HLGA-10_2x2mm_P0.5mm_LayoutBorder3x2y x 2
ST_HLGA-10_2.5x2.5mm_P0.6mm_LayoutBorder3x2y x 2
LQFP-100_14x14mm_P0.5mm
Crystal_SMD_3225-4Pin_3.2x2.5mm
R_0603_1608Metric
D_SOD-123
DF40GB-70DP-0.4V
stigma_core_board_PCB

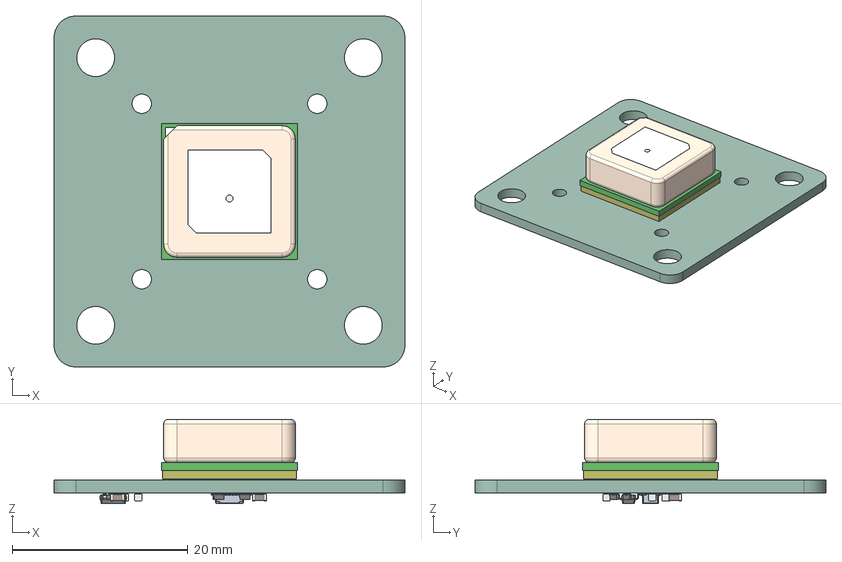
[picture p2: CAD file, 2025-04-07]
stigma_gps_board/stigma_gps_board.step
40.0 x 40.0 x 9.58 mm
SAM-M8Q-0-10_22
SAM-M8Q-0-10_14
SAM-M8Q-0-10_24
SAM-M8Q-0-10_13
SAM-M8Q-0-10_11
SAM-M8Q-0-10_16
SAM-M8Q-0-10_20
SAM-M8Q-0-10_3
SAM-M8Q-0-10_25
SAM-M8Q-0-10_5
SAM-M8Q-0-10_21
SAM-M8Q-0-10_12
SAM-M8Q-0-10_9
SAM-M8Q-0-10_8
SAM-M8Q-0-10_10
SAM-M8Q-0-10_15
SAM-M8Q-0-10_2
SAM-M8Q-0-10_7
SAM-M8Q-0-10
SAM-M8Q-0-10_6
SAM-M8Q-0-10_1
SAM-M8Q-0-10_18
SAM-M8Q-0-10_17
SAM-M8Q-0-10_23
SAM-M8Q-0-10_4
SAM-M8Q-0-10_19
L_0603_1608Metric x 2
C_0603_1608Metric x 5
D_SOD-523 x 4
TSOP-5_1.65x3.05mm_P0.95mm
stigma_gps_board 1.13
stigma_gps_board_PCB

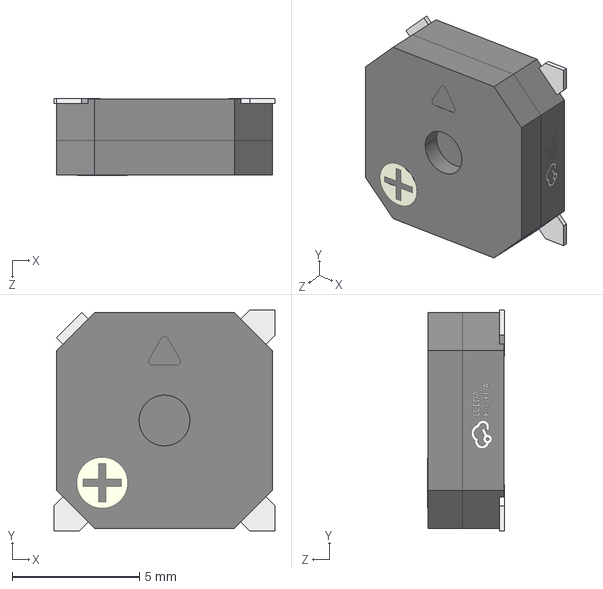
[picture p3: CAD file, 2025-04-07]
common/3dmodels/BUZ-SMD_4P-L8.5-W8.5-H3.0.step
8.70 x 8.70 x 3.02 mm

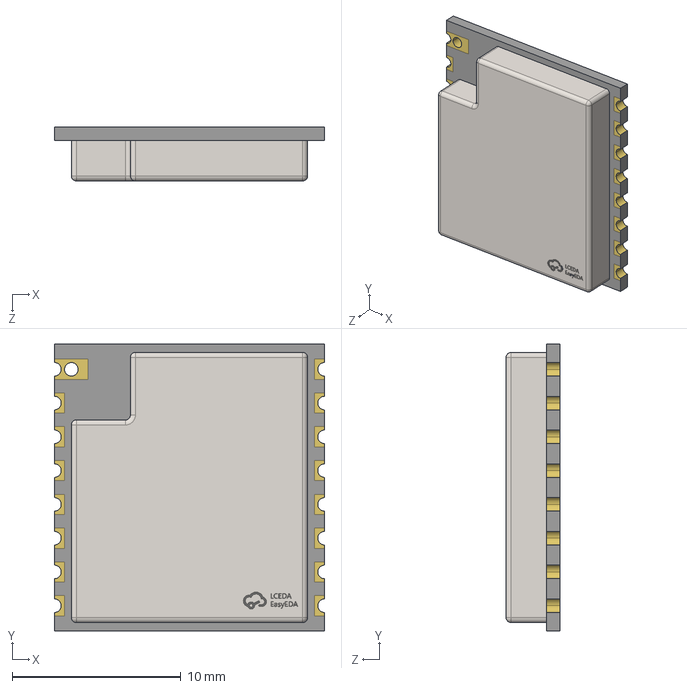
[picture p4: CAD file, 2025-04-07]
common/3dmodels/COMM-SMD_L17.0-W16.0-H3.2-RA-01S (1).step
16.0 x 17.0 x 3.21 mm

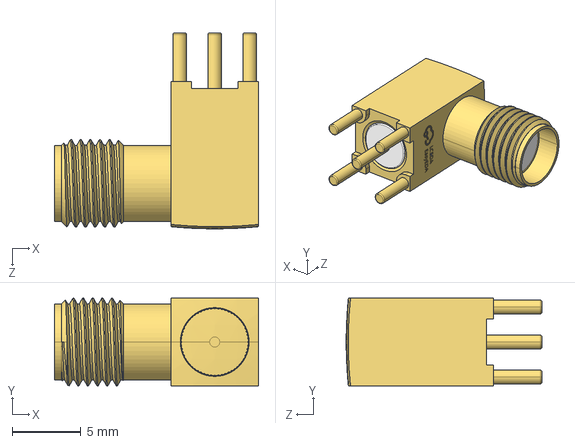
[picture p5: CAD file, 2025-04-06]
common/3dmodels/ANT-TH_L14.8-W6.4-H10.0.step
14.8 x 6.35 x 14.2 mm

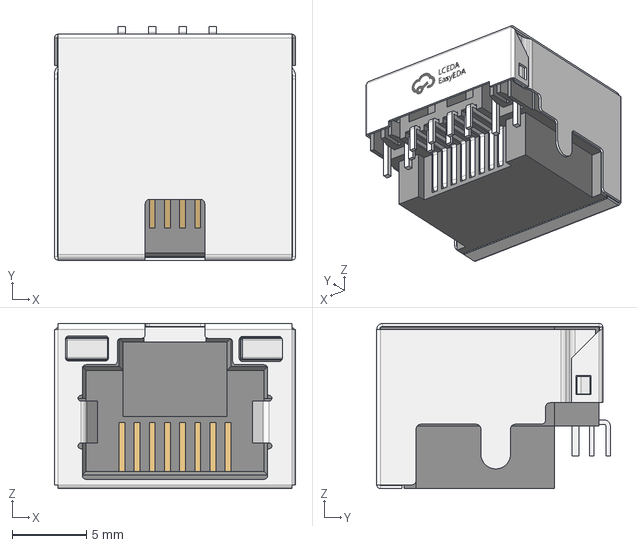
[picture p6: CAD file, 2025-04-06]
common/3dmodels/RJ45-TH_MJ88B-B011-RVL11-P.step
16.2 x 15.7 x 11.1 mm
PRT0001
PRT0002

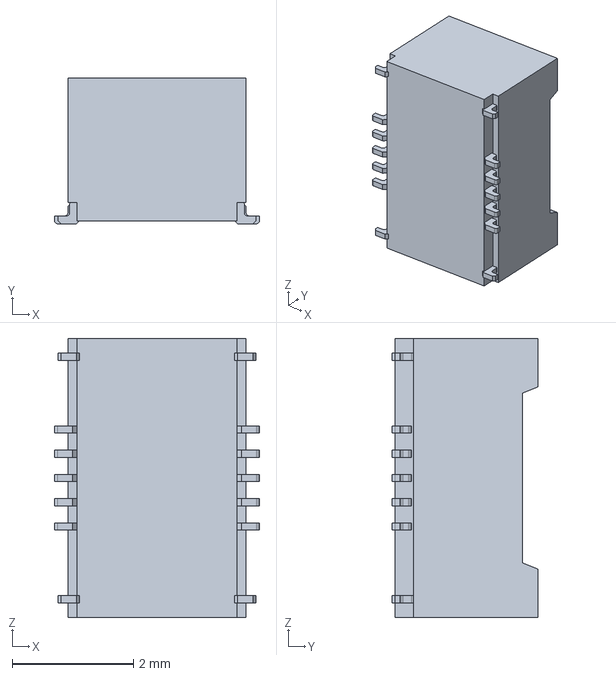
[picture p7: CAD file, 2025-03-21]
common/3dmodels/df40hb_2_5_-10ds-0_4v_51_.stp
3.38 x 2.40 x 4.60 mm

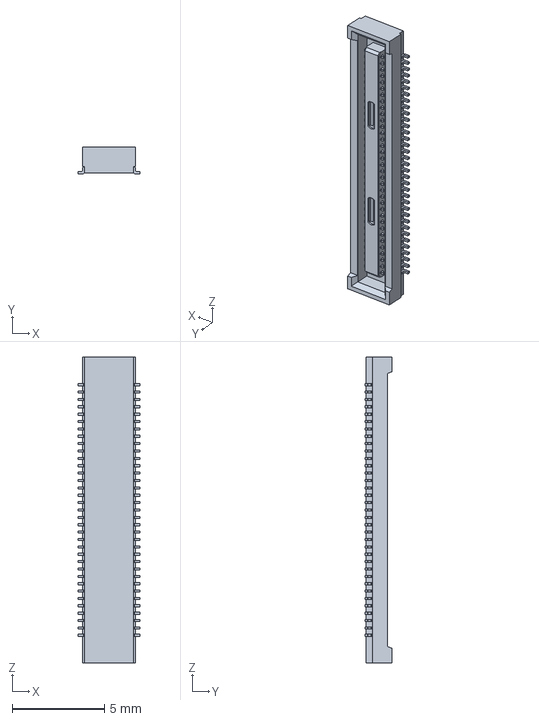
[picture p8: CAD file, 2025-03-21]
common/3dmodels/df40c-70ds-0_4v_51_.stp
3.38 x 1.45 x 16.6 mm

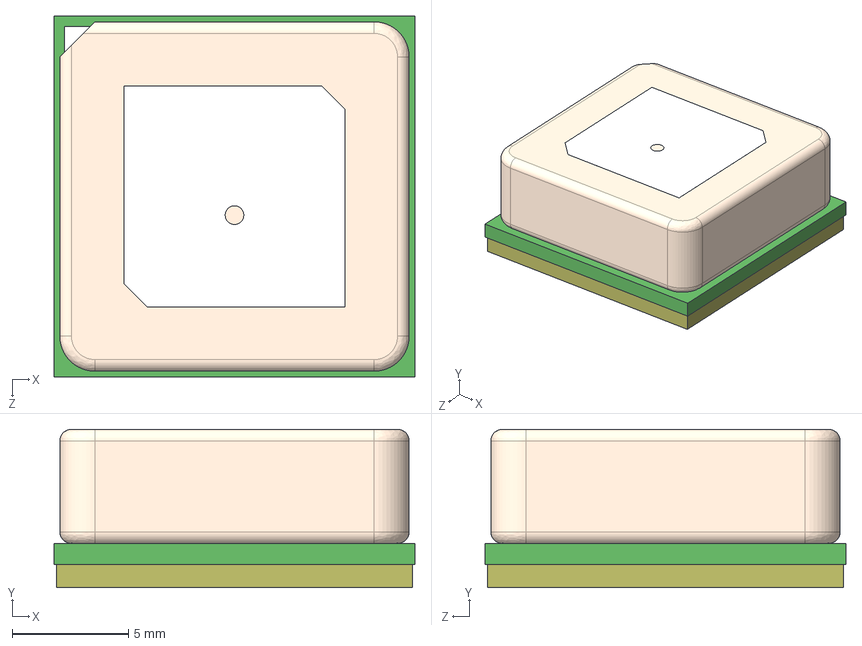
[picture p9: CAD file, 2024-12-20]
common/3dmodels/SAM-M8Q-0.stp
15.5 x 6.80 x 15.5 mm
SAM-M8Q-0-10_22
SAM-M8Q-0-10_14
SAM-M8Q-0-10_24
SAM-M8Q-0-10_13
SAM-M8Q-0-10_11
SAM-M8Q-0-10_16
SAM-M8Q-0-10_20
SAM-M8Q-0-10_3
SAM-M8Q-0-10_25
SAM-M8Q-0-10_5
SAM-M8Q-0-10_21
SAM-M8Q-0-10_12
SAM-M8Q-0-10_9
SAM-M8Q-0-10_8
SAM-M8Q-0-10_10
SAM-M8Q-0-10_15
SAM-M8Q-0-10_2
SAM-M8Q-0-10_7
SAM-M8Q-0-10
SAM-M8Q-0-10_6
SAM-M8Q-0-10_1
SAM-M8Q-0-10_18
SAM-M8Q-0-10_17
SAM-M8Q-0-10_23
SAM-M8Q-0-10_4
SAM-M8Q-0-10_19

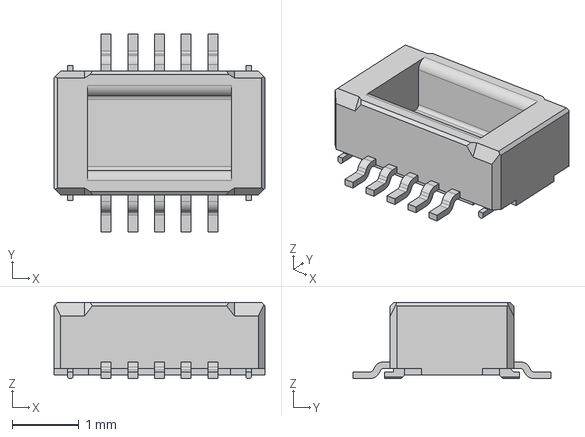
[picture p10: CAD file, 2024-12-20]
common/3dmodels/DF40GB-10DP-0.4V.igs
3.16 x 2.97 x 1.14 mm

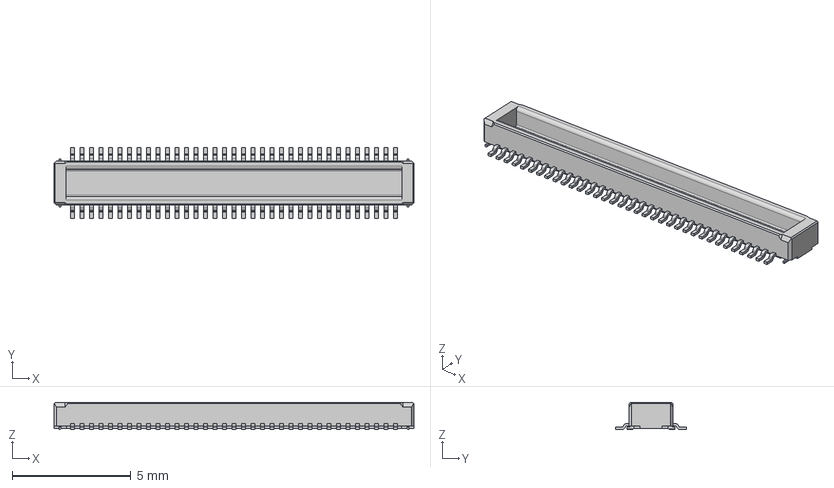
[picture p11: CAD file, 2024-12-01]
common/3dmodels/DF40GB-70DP-0.4V.stp
15.2 x 2.97 x 1.14 mm

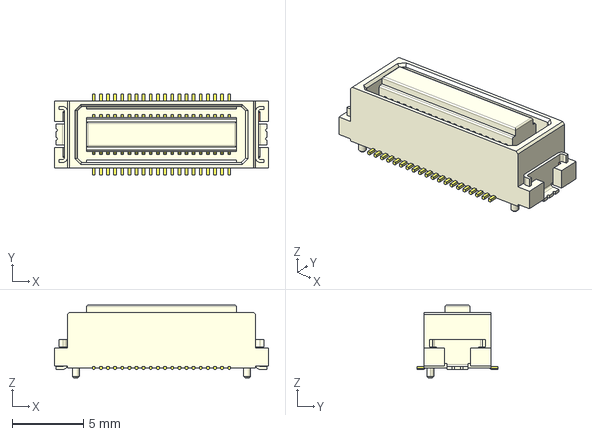
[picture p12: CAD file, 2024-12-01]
common/3dmodels/DF17(4_0)-40DS-0_5V.stp
15.0 x 5.70 x 5.10 mm

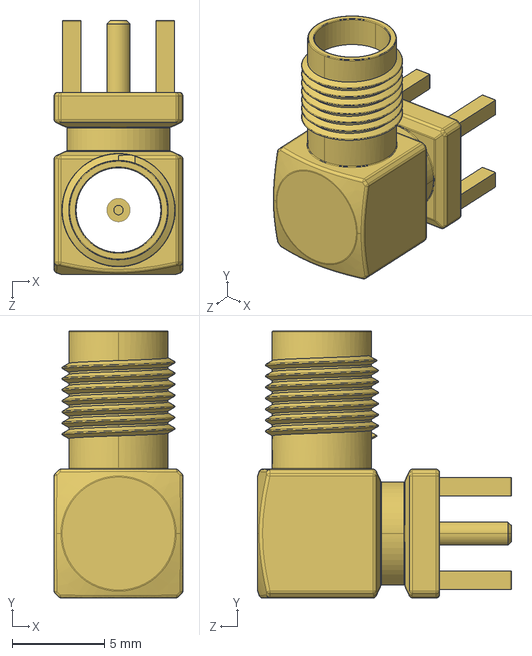
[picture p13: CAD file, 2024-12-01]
common/3dmodels/sma.step
7.00 x 14.5 x 13.8 mm

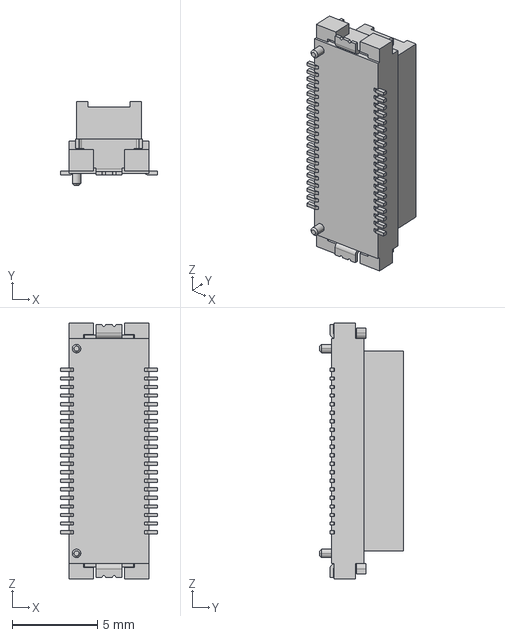
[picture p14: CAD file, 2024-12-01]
common/3dmodels/DF17(2_0)-40DP-0_5V.stp
5.70 x 4.90 x 15.0 mm

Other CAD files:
common/3dmodels/EVQ-PUC02K.step
common/3dmodels/DF17(4_0)-40DP-0_5V.stp
common/3dmodels/sam_m8q.step
common/3dmodels/ra_02.step
common/3dmodels/430450400.step
common/3dmodels/430450800.stp
common/3dmodels/66200821022.stp
common/3dmodels/66201021022.stp
common/3dmodels/66201221022.stp
common/3dmodels/7499010211A.stp
common/3dmodels/dm3at.step
common/3dmodels/usb_c.step

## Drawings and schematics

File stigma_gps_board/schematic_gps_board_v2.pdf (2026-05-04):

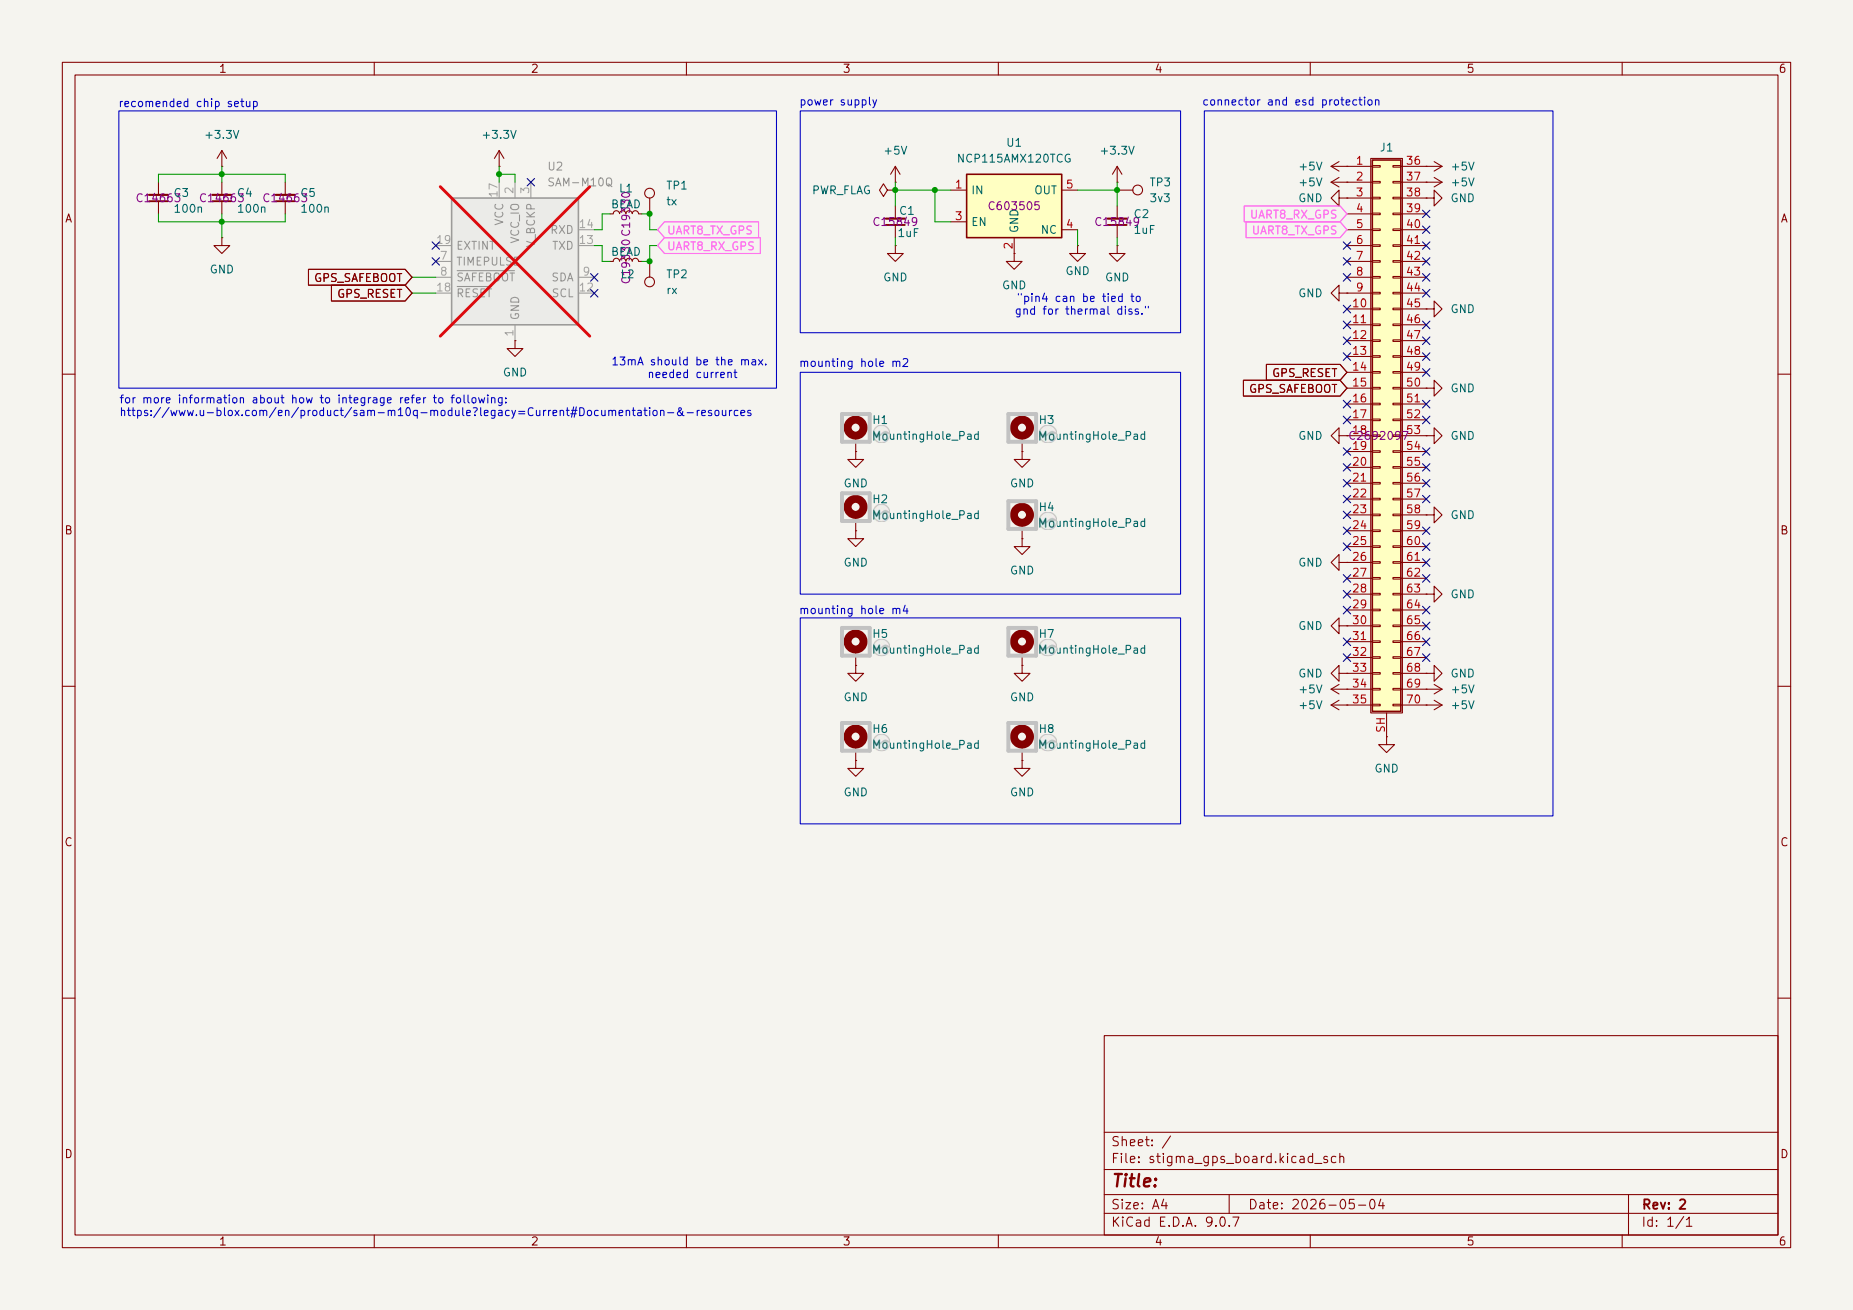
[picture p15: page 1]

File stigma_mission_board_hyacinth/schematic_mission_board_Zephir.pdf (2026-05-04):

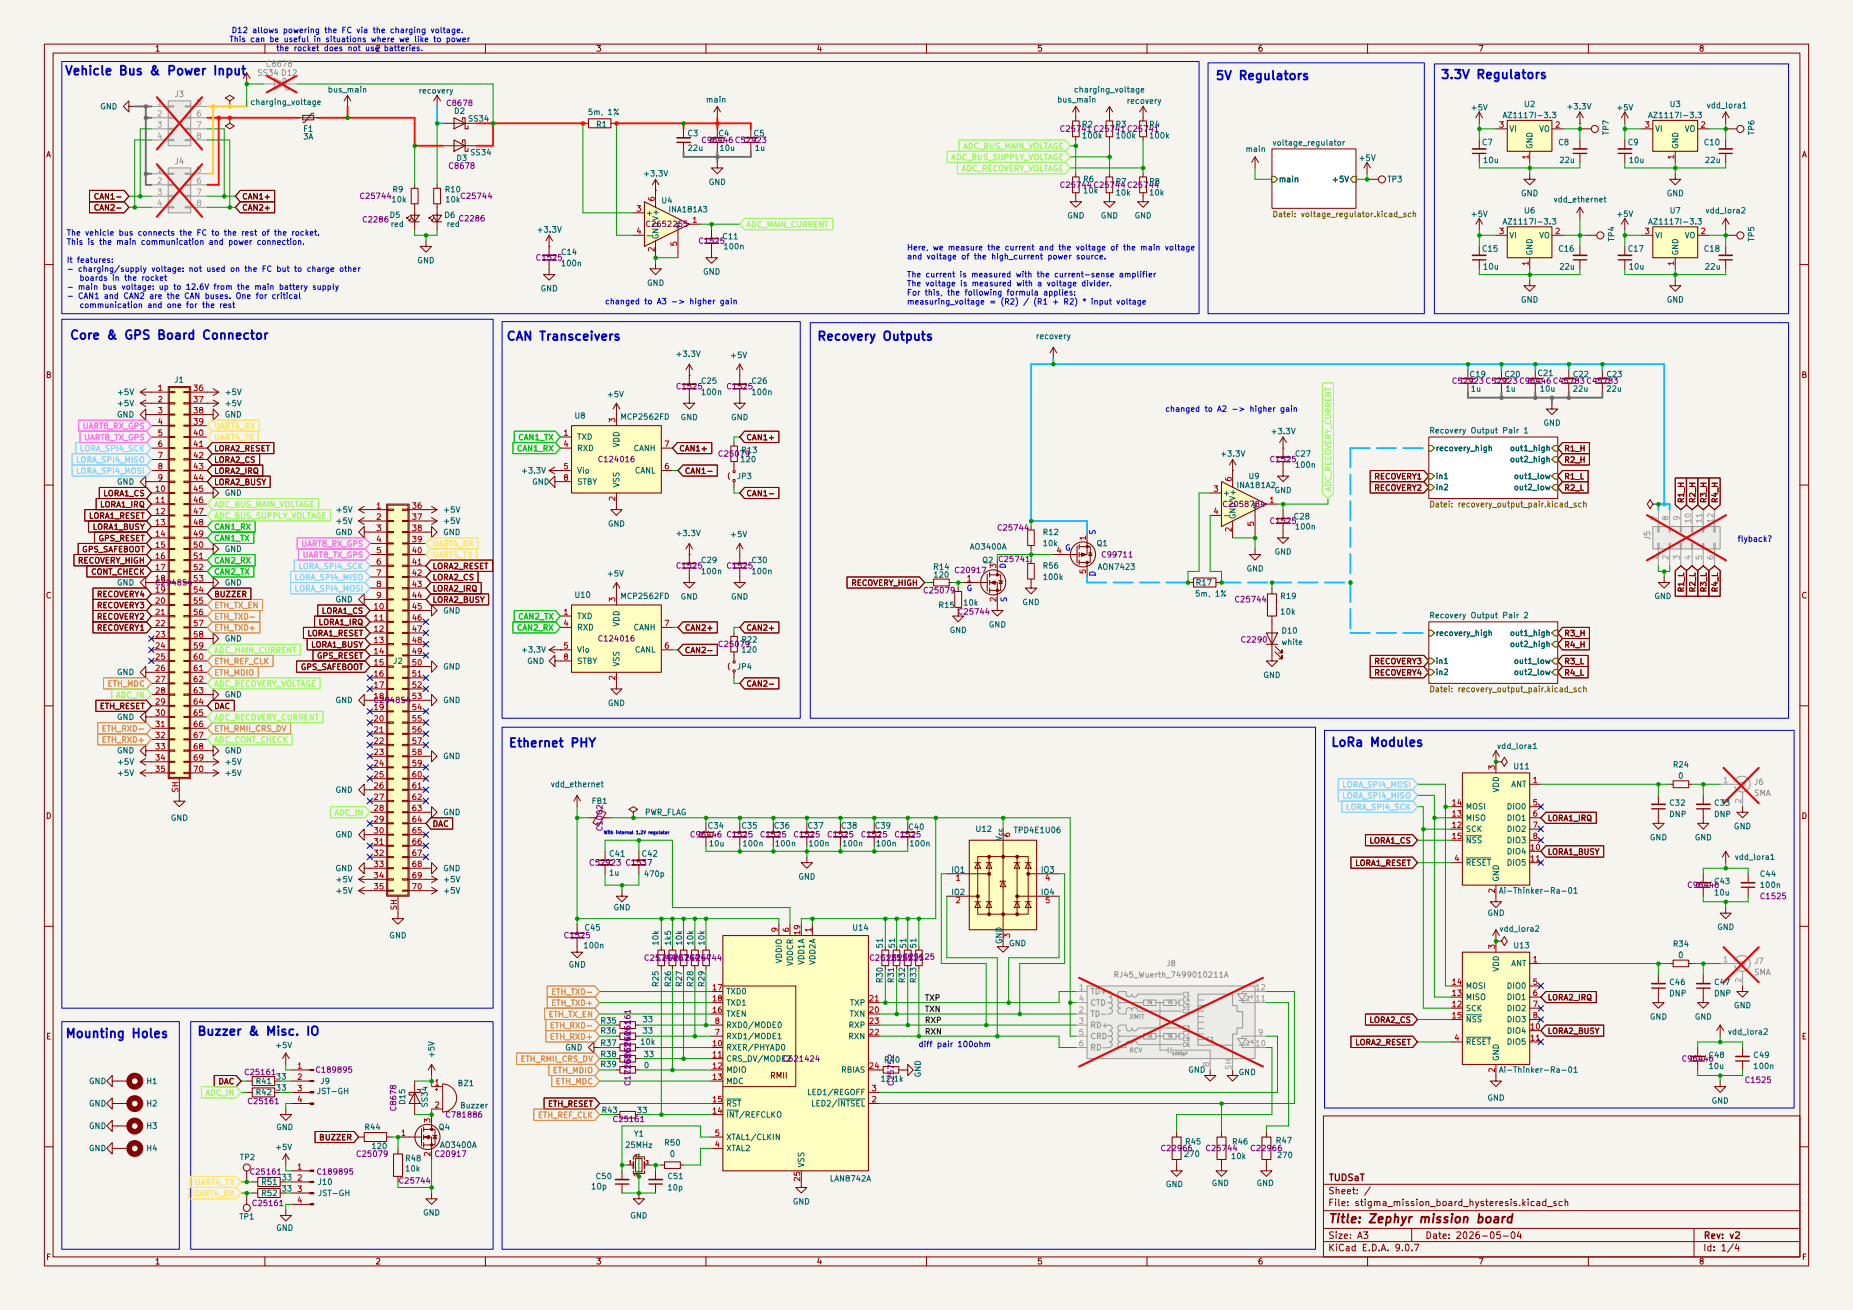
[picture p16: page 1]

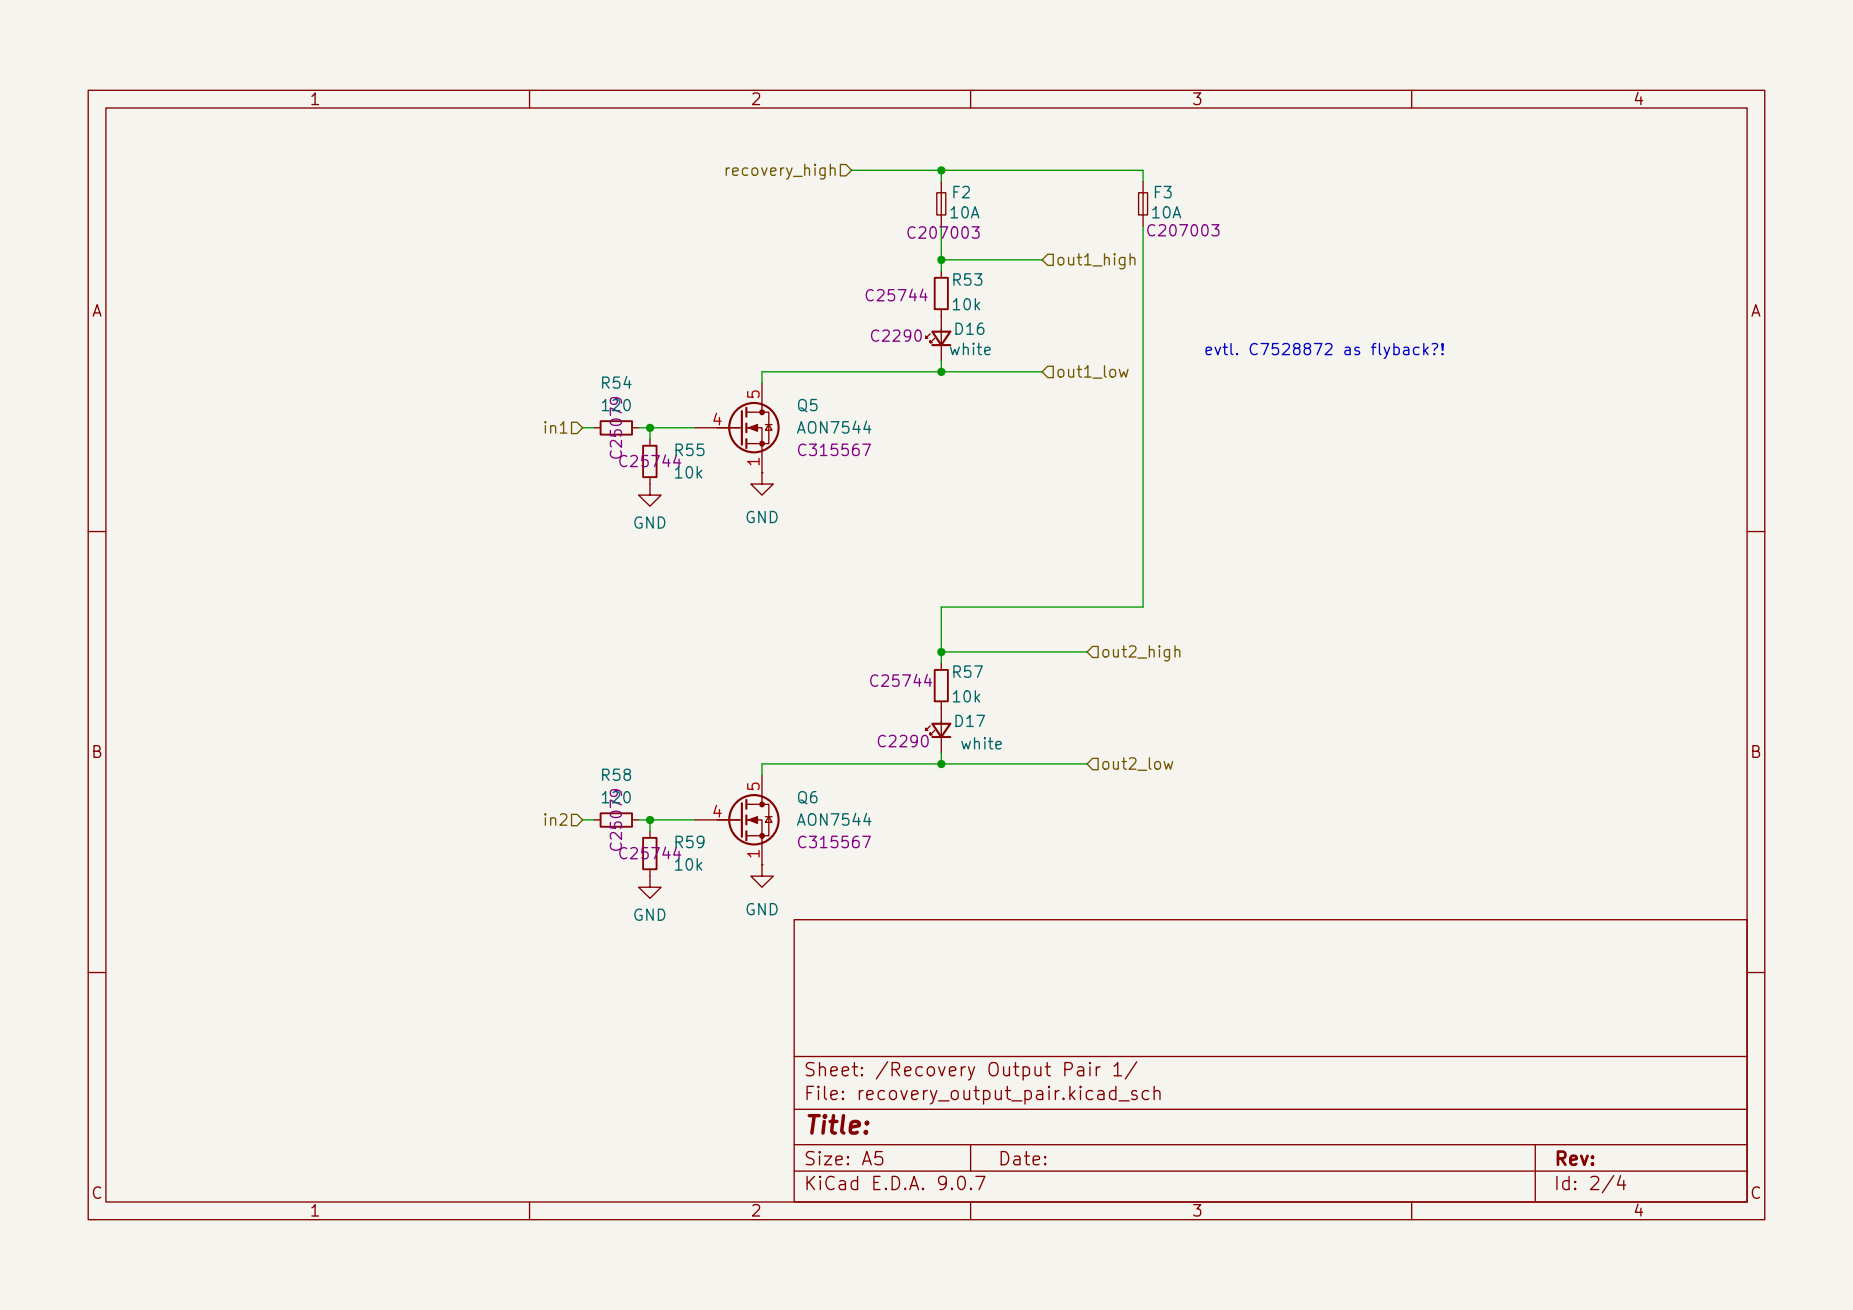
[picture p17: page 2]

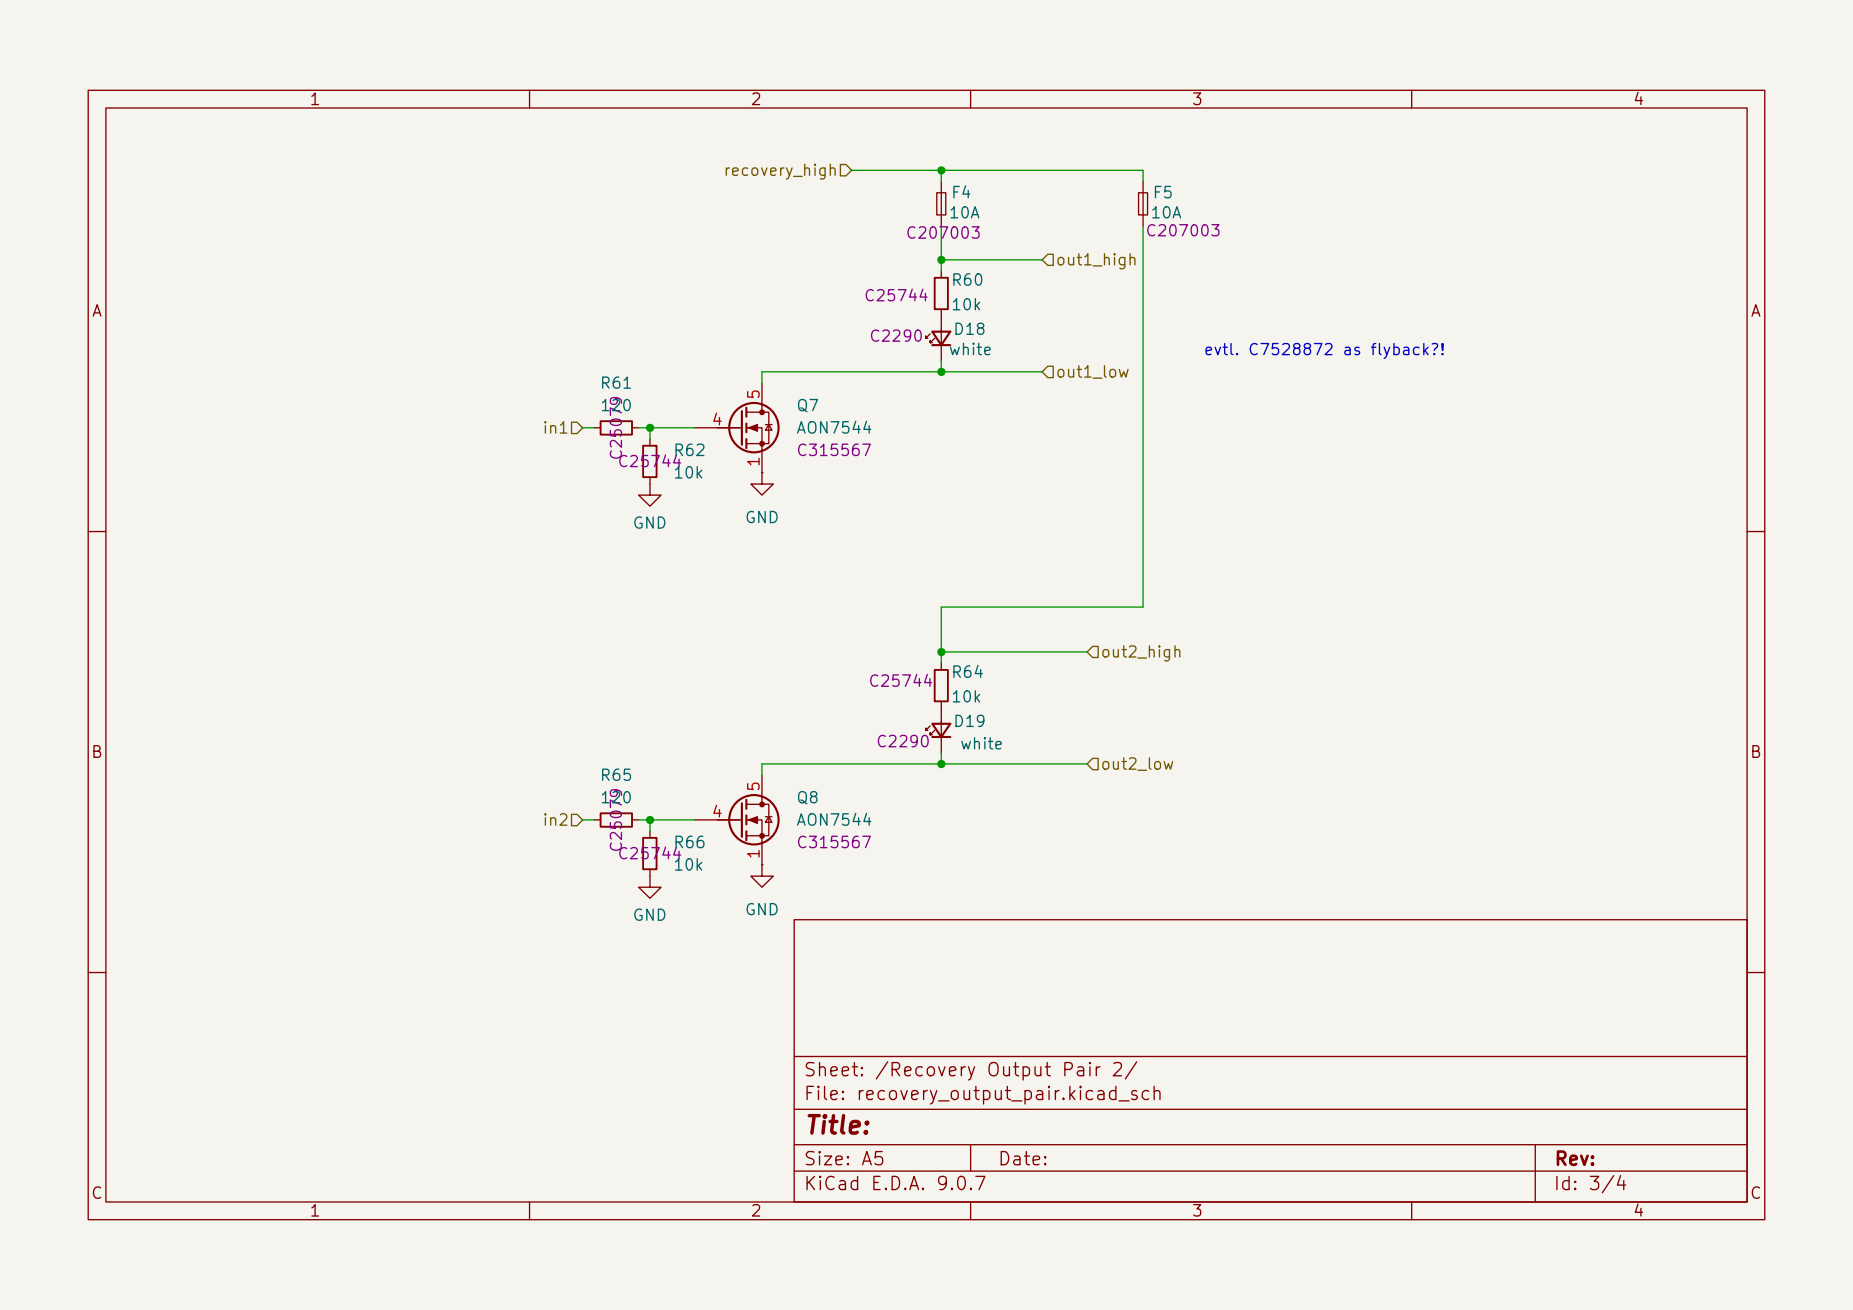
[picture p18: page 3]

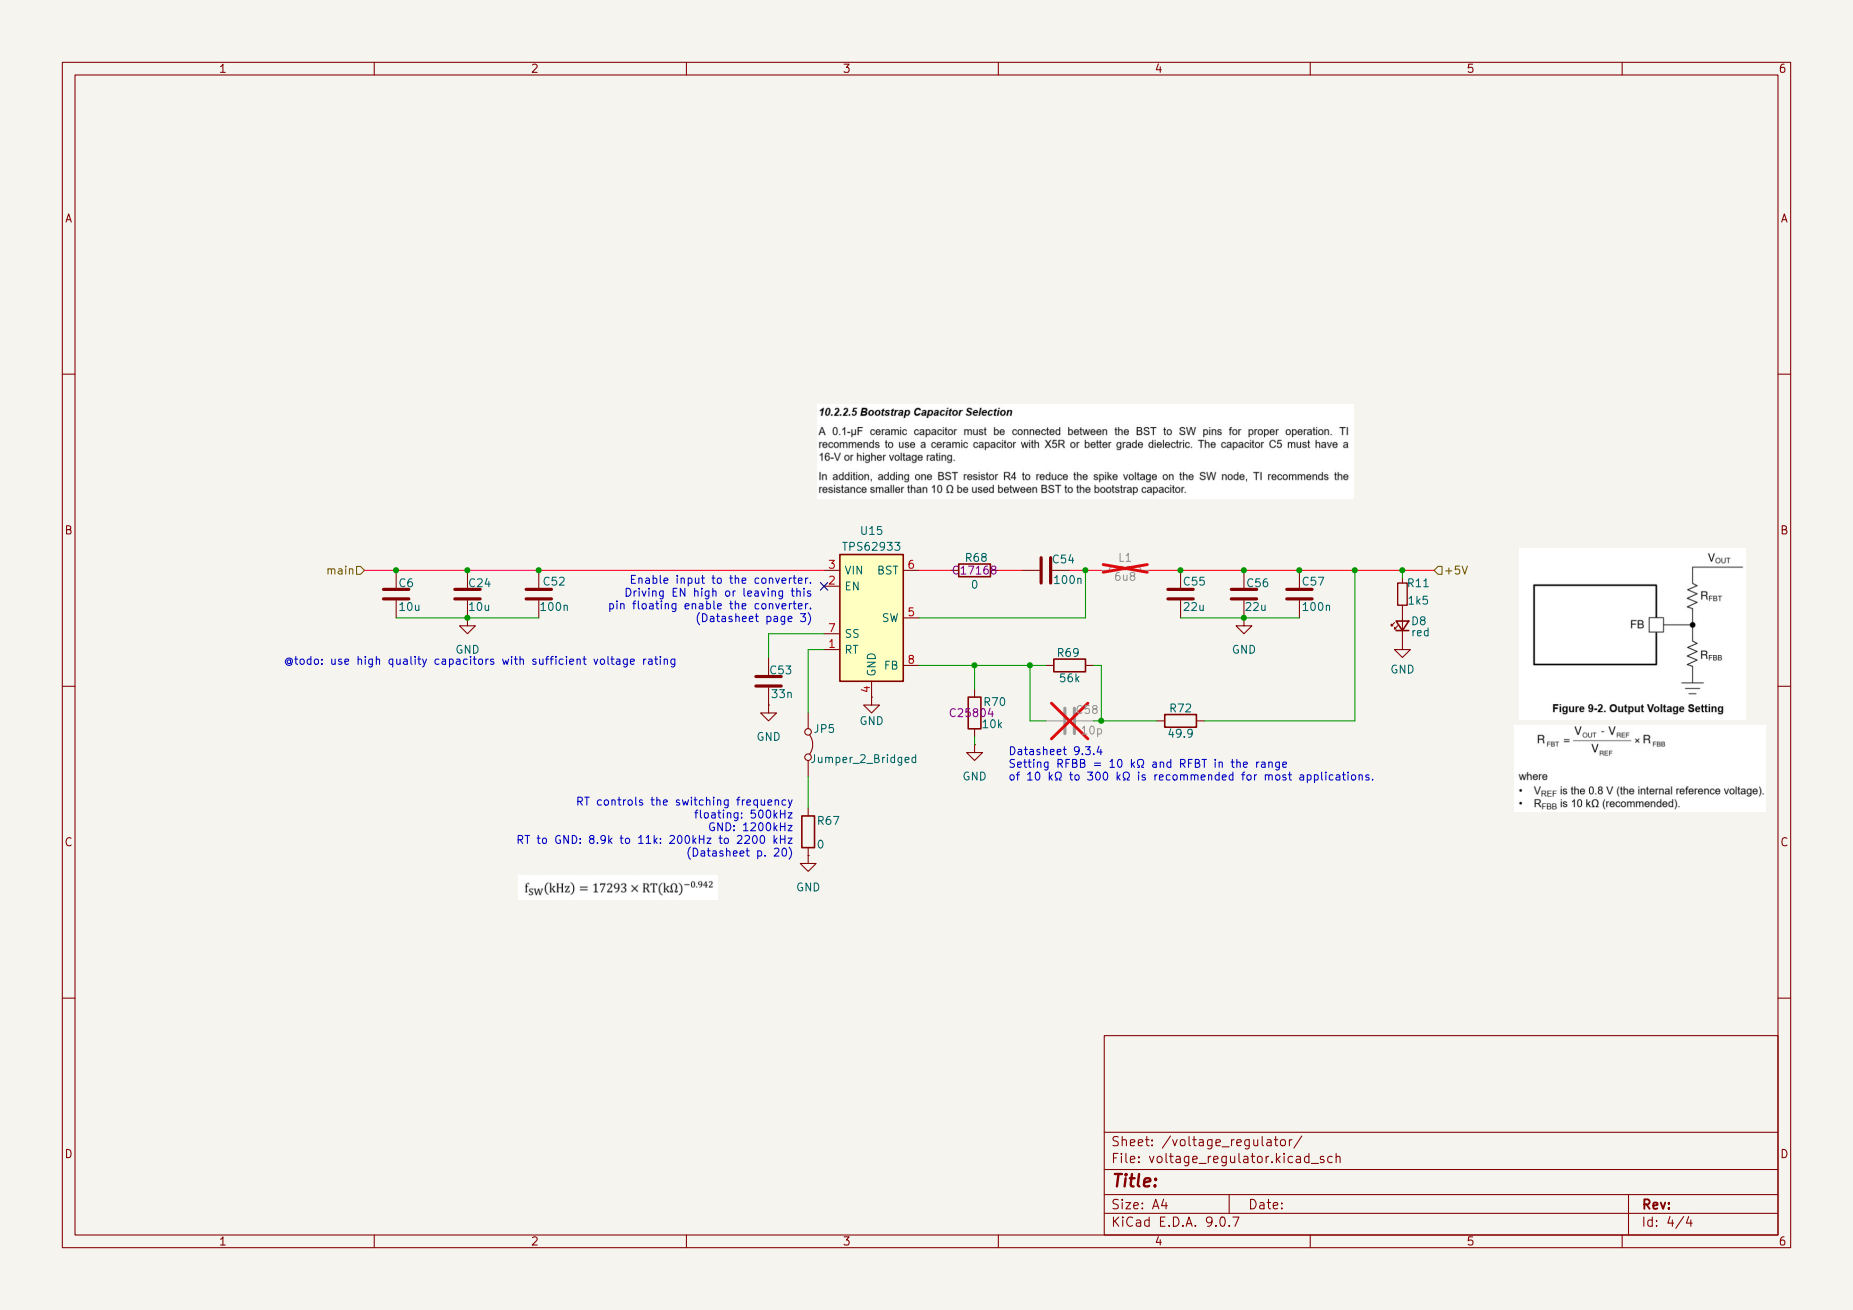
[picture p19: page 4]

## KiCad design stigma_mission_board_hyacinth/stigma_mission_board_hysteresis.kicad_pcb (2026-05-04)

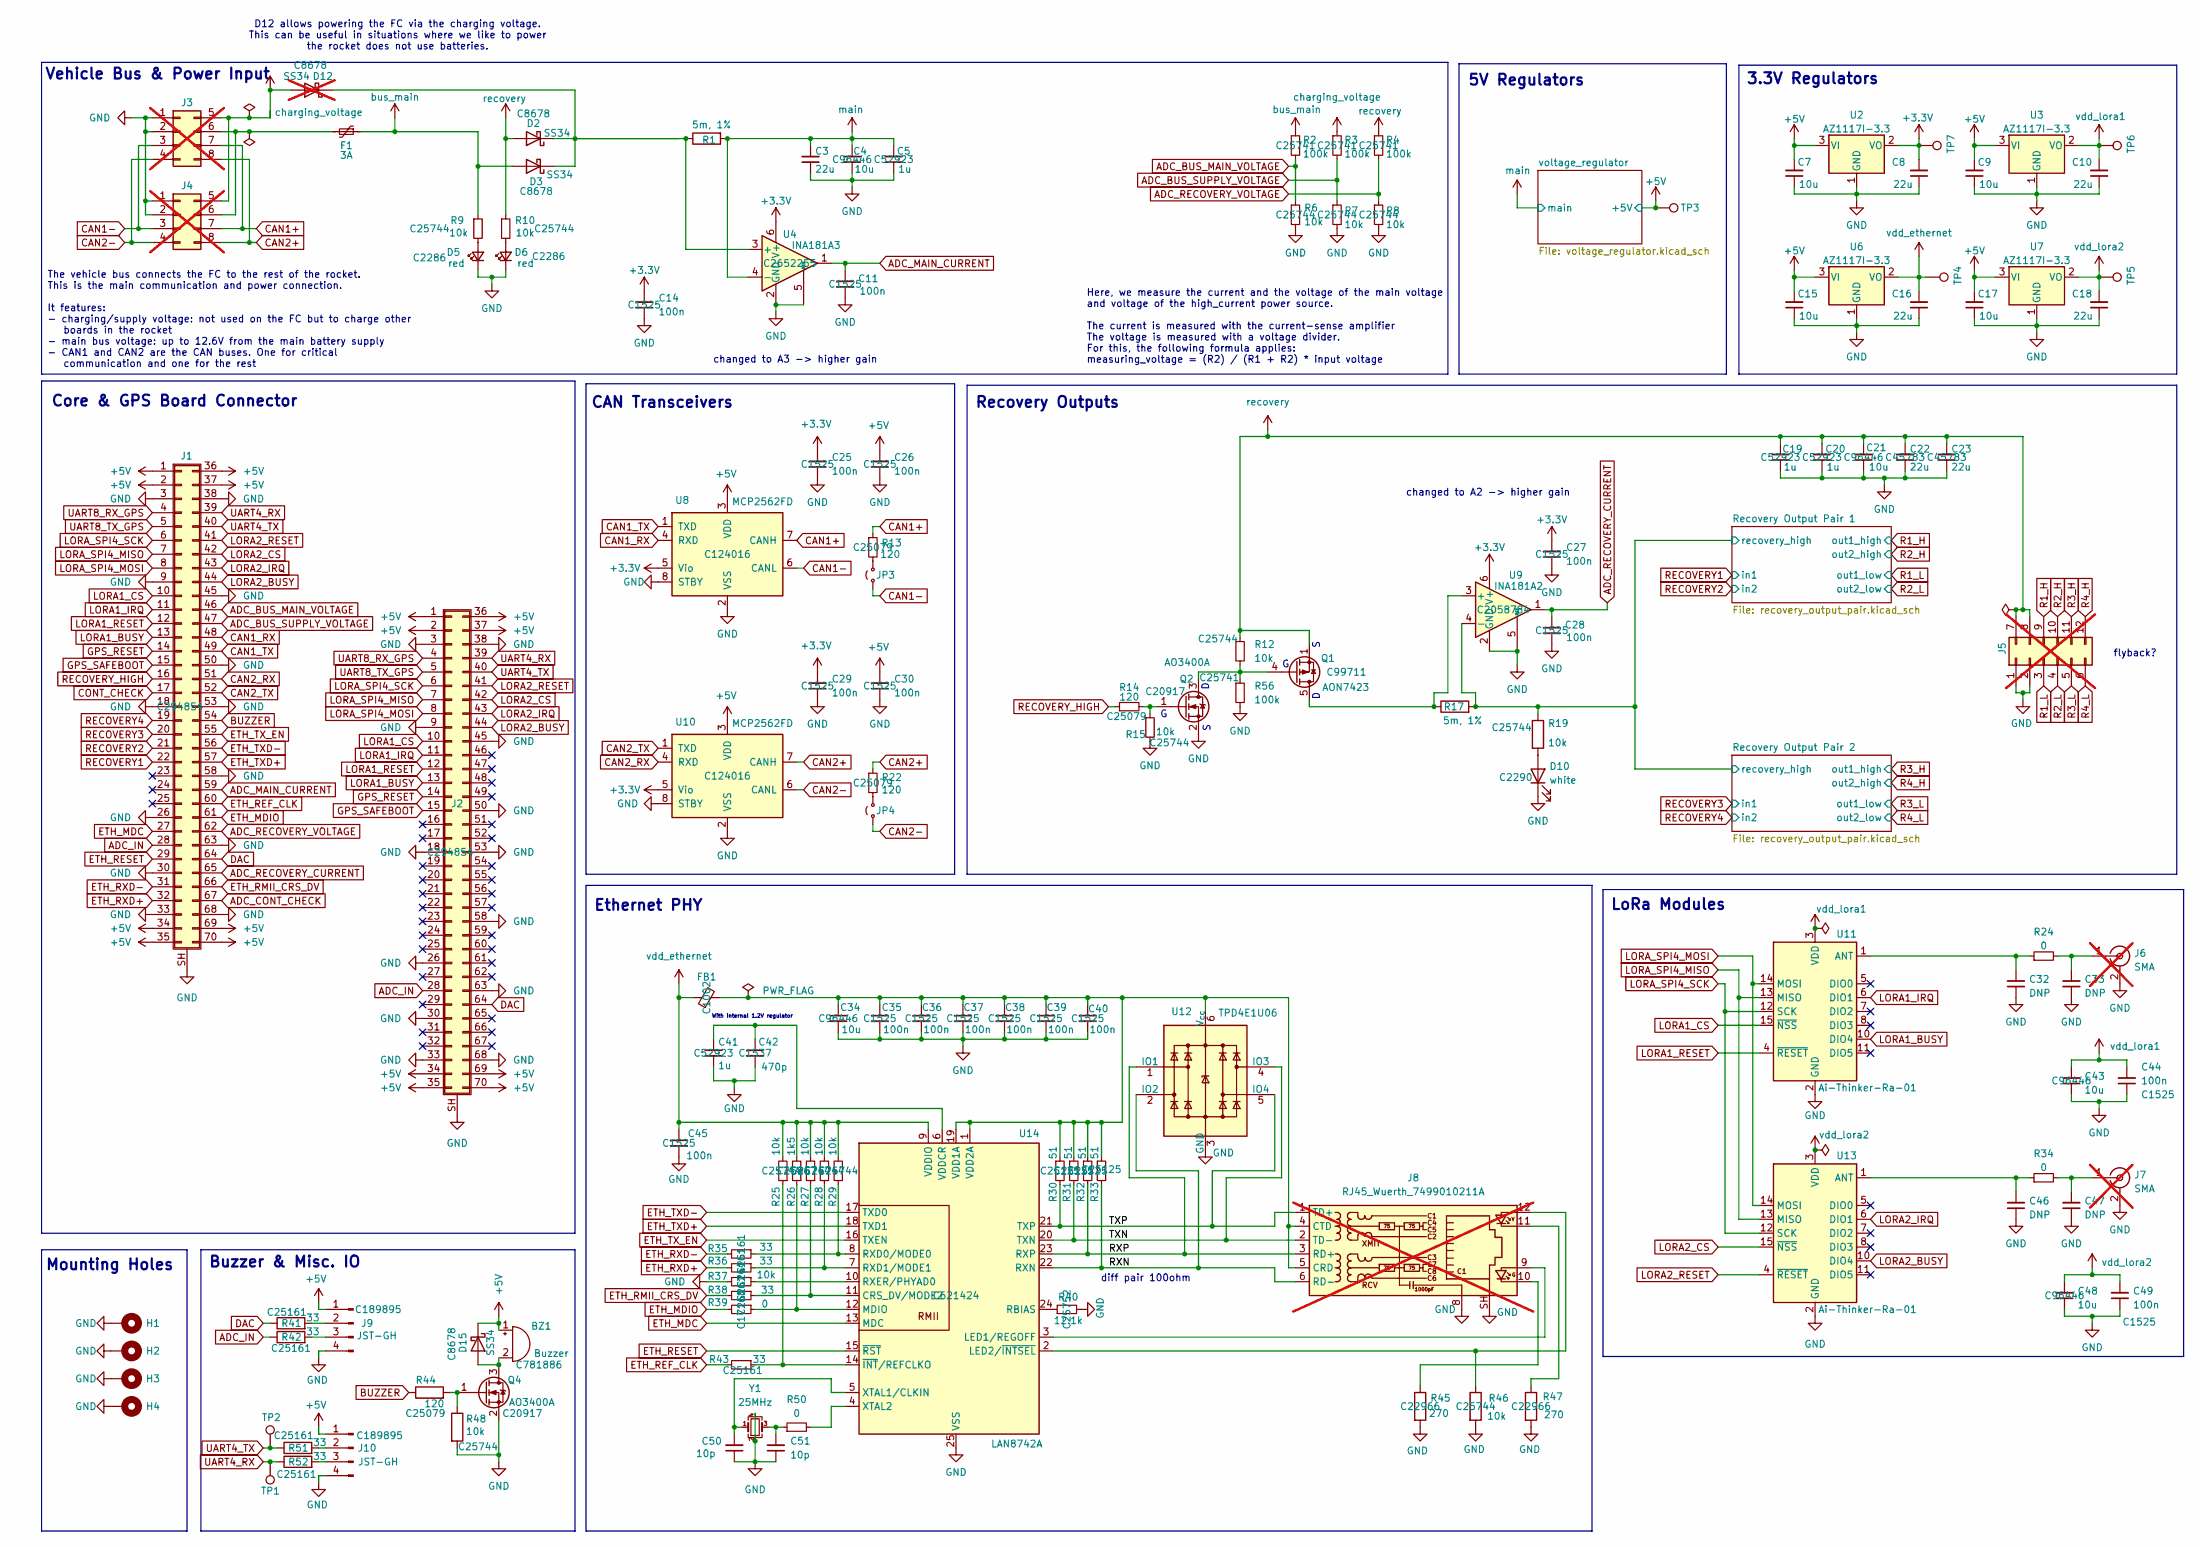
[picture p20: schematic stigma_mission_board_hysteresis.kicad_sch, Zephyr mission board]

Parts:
BZ1: Buzzer; MagneticBuzzer_CUI_CMT-8504-100-SMT; Part# CMT-8504-100-SMT-TR; DigiKey# 102-CMT-8504-100-SMT-CT-ND
C3: 22u; C_0805_2012Metric; LCSC C45783
C4, C21: 10u; C_0603_1608Metric; Part# CS2012X7R106M100NRE; LCSC C96446
C5, C19, C20: 1u; C_0402_1005Metric; Part# CS1608X5R105K250NRB; LCSC C52923
C7, C9, C15, C17, C43, C48: 10u; C_0603_1608Metric; Part# CL31B106KAHNNNE; LCSC C96446
C8, C10, C16, C18: 22u; C_0805_2012Metric; Part# CL31A226KAHNNNE; LCSC C45783
C11, C14, C25, C26, C27, C28, C29, C30, C35, C36, C37, C38, C39, C40, C45: 100n; C_0402_1005Metric; LCSC C1525
C22, C23: 22u; C_0805_2012Metric; Part# CS2012X5R226M250NRE; LCSC C45783
C32, C33, C46, C47: DNP; C_0603_1608Metric
C34: 10u; C_0603_1608Metric; LCSC C96446
C41: 1u; C_0402_1005Metric; LCSC C52923
C42: 470p; C_0402_1005Metric; LCSC C1537
C44, C49: 100n; C_0402_1005Metric; Part# CL10B104KB8NNNC; LCSC C1525
C50, C51: 10p; C_0402_1005Metric; LCSC C32949
D2, D3, D15: SS34; D_SMA; LCSC C8678
D5, D6: red; LED_0603_1608Metric; LCSC C2286
D10: white; LED_0603_1608Metric; LCSC C2290
D12: SS34; D_SMA; LCSC C8678; not fitted
F1: 3A; Fuse_1206_3216Metric_Pad1.42x1.75mm_HandSolder; Part# 0467003.NRHF; LCSC C2838898
FB1: FerriteBead; L_0603_1608Metric; LCSC C1002
H1, H2, H3, H4: MountingHole_Pad; MountingHole_3.2mm_M3_Pad_Via; Part# N/A; DigiKey# N/A
J1, J2: DF40C-70DS-0.4V(51); core-board-inner-mounting-holes; LCSC C294854
J3, J4: Molex_Micro-Fit_3.0_43045-0800_2x04_P3.00mm_Horizontal; not fitted
J5: Molex_Micro-Fit_3.0_43045-1200_2x06_P3.00mm_Horizontal; not fitted
J6, J7: SMA; SMA_Amphenol_132289_EdgeMount; not fitted
J8: RJ45_Wuerth_7499010211A; RJ45_Wuerth_7499010211A_Horizontal; not fitted
J9, J10: JST-GH; JST_GH_SM04B-GHS-TB_1x04-1MP_P1.25mm_Horizontal; LCSC C189895
JP3, JP4: Jumper_2_Small_Open; PinHeader_1x02_P1.27mm_Vertical
Q1: AON7423; DFN-8-1EP_3x3mm_P0.65mm_EP1.55x2.4mm; LCSC C99711
Q2, Q4: AO3400A; SOT-23; LCSC C20917
R1, R17: 5m, 1%; R_2512_6332Metric; LCSC C723630
R2, R3, R4: 100k; R_0402_1005Metric; Part# RC0603FR-071K8L; LCSC C25741
R6, R7, R8, R12: 10k; R_0402_1005Metric; Part# RC0603FR-071KL; LCSC C25744
R9, R10: 10k; R_0402_1005Metric; Part# ESR03EZPJ221; LCSC C25744
R13, R22: 120; R_0402_1005Metric; Part# RC0603FR-07120RL; LCSC C25079
R14: 120; R_0402_1005Metric; Part# RC0603FR-071KL; LCSC C25079
R15, R19, R25, R27, R28, R29, R37, R46, R48: 10k; R_0402_1005Metric; LCSC C25744
R24, R34: 0; R_0603_1608Metric; Part# RC0603FR-070RL
R26: 1k5; R_0402_1005Metric; LCSC C25867
R30, R31, R32, R33: 51; R_0402_1005Metric; LCSC C25125
R35, R36, R38, R41, R42, R43, R51, R52: 33; R_0402_1005Metric; LCSC C25161
R39, R50: 0; R_0402_1005Metric; LCSC C17168
R40: 12.1k; R_0402_1005Metric; LCSC C25752
R44: 120; R_0402_1005Metric; LCSC C25079
R45, R47: 270; R_0603_1608Metric; LCSC C22966
R56: 100k; R_0402_1005Metric; Part# RC0603FR-071KL; LCSC C25741
TP1, TP2, TP3, TP4, TP5, TP6, TP7: TestPoint; TestPoint_Pad_D1.5mm
U2, U3, U6, U7: AZ1117I-3.3; SOT-223-3_TabPin2; Part# AZ1117CH-3.3TRG1; LCSC C92102
U4: INA181A3; SOT-23-6; LCSC C2652255
U8, U10: MCP2562FD; SOIC-8_3.9x4.9mm_P1.27mm; LCSC C124016
U9: INA181A2; SOT-23-6; LCSC C2058784
U11, U13: Ai-Thinker-Ra-01; Ai-Thinker-Ra-01-LoRa
U12: TPD4E1U06; SOT-563; LCSC C527516
U14: LAN8742A; VQFN-24-1EP_4x4mm_P0.5mm_EP2.5x2.5mm_ThermalVias; LCSC C621424
Y1: 25MHz; Crystal_SMD_3225-4Pin_3.2x2.5mm; LCSC C9006

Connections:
+3.3V: C8.2, C14.2, C25.2, C27.2, C29.2, TP7.1, U2.2 (VO), U4.6 (V+), U8.5 (Vio), U9.6 (V+), U10.5 (Vio)
+5V: BZ1.1 (-), C7.2, C9.2, C15.2, C17.2, C26.2, C30.2, D15.1 (K), J1.1, J1.2, J1.34, J1.35, J1.36, J1.37, J1.69, J1.70, J2.1, J2.2, J2.34, J2.35, J2.36, J2.37, J2.69, J2.70, J9.1, J10.1, TP3.1, U2.3 (VI), U3.3 (VI), U6.3 (VI), U7.3 (VI), U8.3 (VDD), U10.3 (VDD); also elsewhere on the board
/RXN: J8.6 (RD-), R33.2, U12.2 (IO2), U14.22 (RXN)
/RXP: J8.3 (RD+), R32.2, U12.1 (IO1), U14.23 (RXP)
/Recovery Output Pair 1/recovery_high: R17.2, R19.1, U9.4 (-); also elsewhere on the board
/TXN: J8.2 (TD-), R31.2, U12.4 (IO3), U14.20 (TXN)
/TXP: J8.1 (TD+), R30.2, U12.5 (IO4), U14.21 (TXP)
ADC_BUS_MAIN_VOLTAGE: J1.46, R2.2, R6.1
ADC_BUS_SUPPLY_VOLTAGE: J1.47, R3.2, R7.1
ADC_CONT_CHECK: J1.67
ADC_IN: J1.28, J2.28, R42.1
ADC_MAIN_CURRENT: C11.1, J1.59, U4.1
ADC_RECOVERY_CURRENT: C28.1, J1.65, U9.1
ADC_RECOVERY_VOLTAGE: J1.62, R4.2, R8.1
BUZZER: J1.54, R44.1
CAN1+: J3.7, J4.7, R13.1, U8.7 (CANH)
CAN1-: J3.3, J4.3, JP3.1 (A), U8.6 (CANL)
CAN1_RX: J1.48, U8.4 (RXD)
CAN1_TX: J1.49, U8.1 (TXD)
CAN2+: J3.8, J4.8, R22.1, U10.7 (CANH)
CAN2-: J3.4, J4.4, JP4.1 (A), U10.6 (CANL)
CAN2_RX: J1.51, U10.4 (RXD)
CAN2_TX: J1.52, U10.1 (TXD)
CONT_CHECK: J1.17
DAC: J1.64, J2.64, R41.1
ETH_MDC: J1.27, U14.13 (MDC)
ETH_MDIO: J1.61, R39.2
ETH_REF_CLK: J1.60, R43.2
ETH_RESET: J1.29, U14.15 (~RST)
ETH_RMII_CRS_DV: J1.66, R38.2
ETH_RXD+: J1.32, R36.2
ETH_RXD-: J1.31, R35.2
ETH_TXD+: J1.57, U14.18 (TXD1)
ETH_TXD-: J1.56, U14.17 (TXD0)
ETH_TX_EN: J1.55, U14.16 (TXEN)
GND: C3.1, C4.1, C5.1, C7.1, C8.1, C9.1, C10.1, C11.2, C14.1, C15.1, C16.1, C17.1, C18.1, C19.1, C20.1, C21.1, C22.1, C23.1, C25.1, C26.1, C27.1, C28.2, C29.1, C30.1, C32.1, C33.1, C34.2, C35.2, C36.2, C37.2, C38.2, C39.2, C40.2, C41.2, C42.2, C43.1, C44.1, C45.2, C46.1, C47.1, C48.1, C49.1, C50.1, C51.1, D5.1 (K), D6.1 (K), D10.1 (K), H1.1, H2.1, H3.1, H4.1, J1.3, J1.9, J1.18, J1.26, J1.30, J1.33, J1.38, J1.45, J1.50, J1.53, J1.58, J1.63, J1.68, J1.SH (Shield), J2.3, J2.9, J2.18, J2.26, J2.30, J2.33, J2.38, J2.45, J2.50, J2.53, J2.58, J2.63, J2.68, J2.SH (Shield), J3.1, J3.2, J4.1, J4.2, J5.1, J5.2, J6.2 (Ext), J7.2 (Ext), J8.8, J8.SH, J9.4, J10.4, Q2.2 (S), Q4.2 (S), R6.2, R7.2, R8.2, R15.2, R37.2, R40.2, R45.2, R46.2, R47.2, R48.2, R56.2, U2.1 (GND), U3.1 (GND), U4.2 (GND), U4.5 (REF), U6.1 (GND), U7.1 (GND), U8.2 (VSS), U8.8 (STBY), U9.2 (GND), U9.5 (REF), U10.2 (VSS), U10.8 (STBY), U11.2 (GND), U11.9 (GND), U11.16 (GND), U12.3 (GND), U13.2 (GND), U13.9 (GND), U13.16 (GND), U14.25 (VSS), Y1.2, Y1.4; also elsewhere on the board
GPS_RESET: J1.14, J2.14
GPS_SAFEBOOT: J1.15, J2.15
LORA1_BUSY: J1.13, J2.13, U11.10 (DIO4)
LORA1_CS: J1.10, J2.10, U11.15 (~NSS)
LORA1_IRQ: J1.11, J2.11, U11.6 (DIO1)
LORA1_RESET: J1.12, J2.12, U11.4 (~RESET)
LORA2_BUSY: J1.44, J2.44, U13.10 (DIO4)
LORA2_CS: J1.42, J2.42, U13.15 (~NSS)
LORA2_IRQ: J1.43, J2.43, U13.6 (DIO1)
LORA2_RESET: J1.41, J2.41, U13.4 (~RESET)
LORA_SPI4_MISO: J1.7, J2.7, U11.13 (MISO), U13.13 (MISO)
LORA_SPI4_MOSI: J1.8, J2.8, U11.14 (MOSI), U13.14 (MOSI)
LORA_SPI4_SCK: J1.6, J2.6, U11.12 (SCK), U13.12 (SCK)
unnamed: BZ1.2 (+), D15.2 (A), Q4.3 (D)
unnamed: C51.2, R50.1, Y1.3
unnamed: D5.2 (A), R9.2
unnamed: D6.2 (A), R10.2
unnamed: D10.2 (A), R19.2
unnamed: D2.1 (K), D3.1 (K), D12.1 (K), R1.1, U4.3 (+)
unnamed: F1.2, J3.6, J4.6
unnamed: C33.2, J6.1 (In), R24.2
unnamed: C47.2, J7.1 (In), R34.2
unnamed: C34.1, C35.1, C36.1, C37.1, C38.1, C39.1, C40.1, FB1.2, J8.4 (CTD), J8.5 (CRD), R30.1, R31.1, R32.1, R33.1, U12.6 (V_{cc}), U14.1 (VDD2A), U14.19 (VDD1A)
unnamed: J8.10, R45.1
unnamed: J8.11, R47.1
unnamed: J9.2, R41.2
unnamed: J9.3, R42.2
unnamed: J10.2, R51.2
unnamed: J10.3, R52.2
unnamed: JP3.2 (B), R13.2
unnamed: JP4.2 (B), R22.2
unnamed: Q1.4 (G), Q2.3 (D), R12.2, R56.1
unnamed: Q2.1 (G), R14.2, R15.1
unnamed: Q4.1 (G), R44.2, R48.1
unnamed: Q1.5 (D), Q1.6 (D), Q1.7 (D), Q1.8 (D), Q1.9 (D), R17.1, U9.3 (+)
unnamed: C32.2, R24.1, U11.1 (ANT)
unnamed: C46.2, R34.1, U13.1 (ANT)
unnamed: R27.1, R38.1, U14.11 (CRS_DV/MODE2)
unnamed: J8.9, U14.3 (LED1/REGOFF)
unnamed: J8.12, R46.1, U14.2 (LED2/~INTSEL)
unnamed: R26.1, R39.1, U14.12 (MDIO)
unnamed: R40.1, U14.24 (RBIAS)
unnamed: R29.1, R35.1, U14.8 (RXD0/MODE0)
unnamed: R28.1, R36.1, U14.7 (RXD1/MODE1)
unnamed: R37.1, U14.10 (RXER/PHYAD0)
unnamed: C41.1, C42.1, U14.6 (VDDCR)
unnamed: C50.2, U14.5 (XTAL1/CLKIN), Y1.1
unnamed: R50.2, U14.4 (XTAL2)
unnamed: R25.1, R43.1, U14.14 (~INT/REFCLKO)
R1_H: J5.9; also elsewhere on the board
R1_L: J5.3; also elsewhere on the board
R2_H: J5.10; also elsewhere on the board
R2_L: J5.4; also elsewhere on the board
R3_H: J5.11; also elsewhere on the board
R3_L: J5.5; also elsewhere on the board
R4_H: J5.12; also elsewhere on the board
R4_L: J5.6; also elsewhere on the board
RECOVERY1: J1.22; also elsewhere on the board
RECOVERY2: J1.21; also elsewhere on the board
RECOVERY3: J1.20; also elsewhere on the board
RECOVERY4: J1.19; also elsewhere on the board
RECOVERY_HIGH: J1.16, R14.1
UART4_RX: J1.39, J2.39, R52.1, TP1.1
UART4_TX: J1.40, J2.40, R51.1, TP2.1
UART8_RX_GPS: J1.4, J2.4
UART8_TX_GPS: J1.5, J2.5
bus_main: D3.2 (A), F1.1, R2.1, R9.1
charging_voltage: D12.2 (A), J3.5, J4.5, R3.1
main: C3.2, C4.2, C5.2, R1.2, U4.4 (-); also elsewhere on the board
recovery: C19.2, C20.2, C21.2, C22.2, C23.2, D2.2 (A), J5.7, J5.8, Q1.1 (S), Q1.2 (S), Q1.3 (S), R4.1, R10.1, R12.1
vdd_ethernet: C16.2, C45.1, FB1.1, R25.2, R26.2, R27.2, R28.2, R29.2, TP4.1, U6.2 (VO), U14.9 (VDDIO)
vdd_lora1: C10.2, C43.2, C44.2, TP6.1, U3.2 (VO), U11.3 (VDD)
vdd_lora2: C18.2, C48.2, C49.2, TP5.1, U7.2 (VO), U13.3 (VDD)

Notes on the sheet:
Mounting Holes
Here, we measure the current and the voltage of the main voltage and voltage of the high_current power source. The current is measured with the current-sense amplifier The voltage is measured with a voltage divider. For this, the following formula applies: measuring_voltage = (R2) / (R1 + R2) * inp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
diff pair 100ohm
Recovery Outputs
Ethernet PHY
LoRa Modules
5V Regulators
CAN Transceivers
Vehicle Bus & Power Input
3.3V Regulators
Core & GPS Board Connector
D12 allows powering the FC via the charging voltage. This can be useful in situations where we like to power the rocket does not use batteries.
flyback?
The vehicle bus connects the FC to the rest of the rocket. This is the main communication and power connection. It features: - charging/supply voltage: not used on the FC but to charge other boards in the rocket - main bus voltage: up to 12.6V from the main battery supply - CAN1 and CAN2 are the CA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
changed to A2 -> higher gain
Buzzer & Misc. IO
changed to A3 -> higher gain
With internal 1.2V regulator

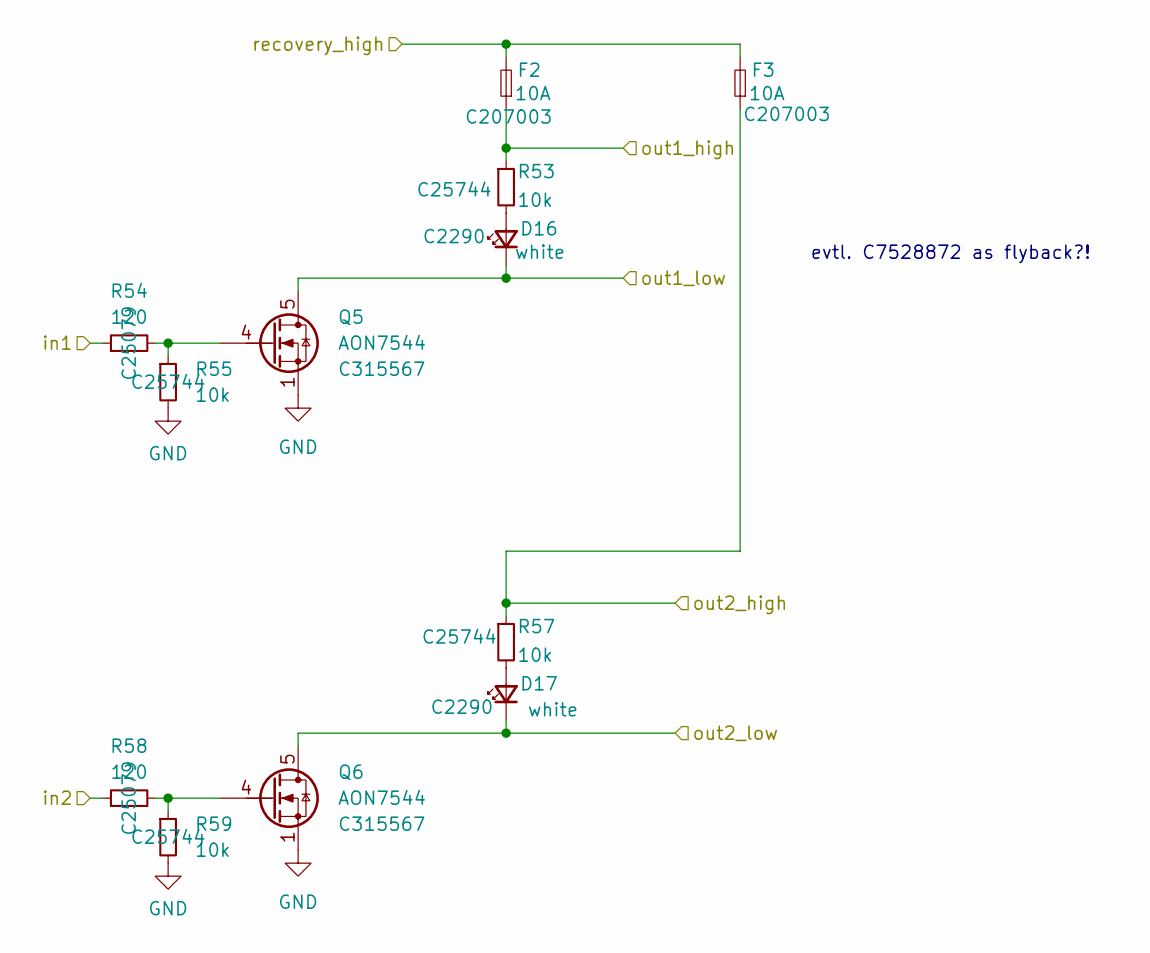
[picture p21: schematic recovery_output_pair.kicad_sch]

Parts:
D16, D17: white; LED_0603_1608Metric; LCSC C2290
F2, F3: 10A; Fuse_1206_3216Metric_Pad1.42x1.75mm_HandSolder; LCSC C207003
Q5, Q6: AON7544; DFN-8-1EP_3x3mm_P0.65mm_EP1.55x2.4mm; LCSC C315567
R53, R55, R57, R59: 10k; R_0402_1005Metric; LCSC C25744
R54, R58: 120; R_0402_1005Metric; LCSC C25079

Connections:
/Recovery Output Pair 1/recovery_high: F2.2, F3.2; also elsewhere on the board
GND: Q5.1 (S), Q5.2 (S), Q5.3 (S), Q6.1 (S), Q6.2 (S), Q6.3 (S), R55.2, R59.2; also elsewhere on the board
unnamed: D16.2 (A), R53.2
unnamed: D17.2 (A), R57.2
unnamed: Q5.4 (G), R54.2, R55.1
unnamed: Q6.4 (G), R58.2, R59.1
R1_H: F2.1, R53.1; also elsewhere on the board
R1_L: D16.1 (K), Q5.5 (D), Q5.6 (D), Q5.7 (D), Q5.8 (D), Q5.9 (D); also elsewhere on the board
R2_H: F3.1, R57.1; also elsewhere on the board
R2_L: D17.1 (K), Q6.5 (D), Q6.6 (D), Q6.7 (D), Q6.8 (D), Q6.9 (D); also elsewhere on the board
RECOVERY1: R54.1; also elsewhere on the board
RECOVERY2: R58.1; also elsewhere on the board

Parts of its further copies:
D18, D19: white; LED_0603_1608Metric; LCSC C2290
F4, F5: 10A; Fuse_1206_3216Metric_Pad1.42x1.75mm_HandSolder; LCSC C207003
Q7, Q8: AON7544; DFN-8-1EP_3x3mm_P0.65mm_EP1.55x2.4mm; LCSC C315567
R60, R62, R64, R66: 10k; R_0402_1005Metric; LCSC C25744
R61, R65: 120; R_0402_1005Metric; LCSC C25079

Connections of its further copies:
/Recovery Output Pair 1/recovery_high: F4.2, F5.2; also elsewhere on the board
GND: Q7.1 (S), Q7.2 (S), Q7.3 (S), Q8.1 (S), Q8.2 (S), Q8.3 (S), R62.2, R66.2; also elsewhere on the board
unnamed: D18.2 (A), R60.2
unnamed: D19.2 (A), R64.2
unnamed: Q7.4 (G), R61.2, R62.1
unnamed: Q8.4 (G), R65.2, R66.1
R3_H: F4.1, R60.1; also elsewhere on the board
R3_L: D18.1 (K), Q7.5 (D), Q7.6 (D), Q7.7 (D), Q7.8 (D), Q7.9 (D); also elsewhere on the board
R4_H: F5.1, R64.1; also elsewhere on the board
R4_L: D19.1 (K), Q8.5 (D), Q8.6 (D), Q8.7 (D), Q8.8 (D), Q8.9 (D); also elsewhere on the board
RECOVERY3: R61.1; also elsewhere on the board
RECOVERY4: R65.1; also elsewhere on the board

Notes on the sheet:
evtl. C7528872 as flyback?!

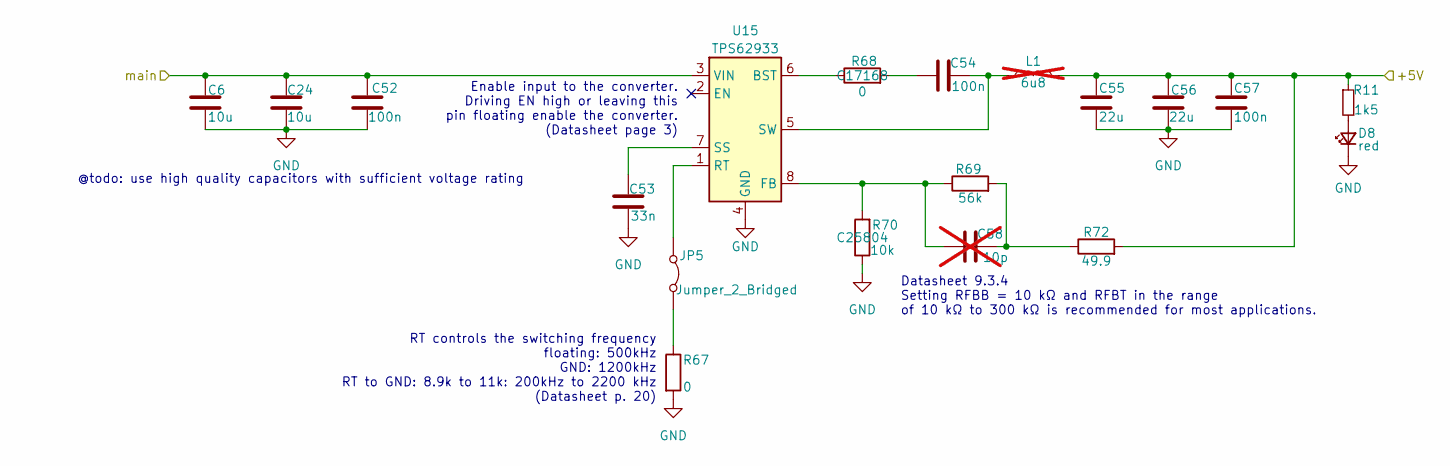
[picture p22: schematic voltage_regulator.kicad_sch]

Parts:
C6, C24: 10u; C_0603_1608Metric; LCSC C19702
C52: 100n; C_0402_1005Metric; LCSC# C1525
C53: 33n; C_0402_1005Metric; LCSC C7419416
C54, C57: 100n; C_0402_1005Metric; LCSC C1525
C55, C56: 22u; C_0603_1608Metric; LCSC C59461
C58: 10p; C_0603_1608Metric; not fitted
D8: red; LED_0603_1608Metric; LCSC C2286
JP5: Jumper_2_Bridged; SolderJumper-2_P1.3mm_Bridged_Pad1.0x1.5mm
L1: 6u8; L_Wuerth_XHMI-6060; not fitted
R11: 1k5; R_0402_1005Metric; Part# ESR03EZPJ221; LCSC C25867
R67: 0; R_0603_1608Metric; LCSC C21189
R68: 0; R_0402_1005Metric; LCSC C17168
R69: 56k; R_0603_1608Metric; LCSC# C23206
R70: 10k; R_0603_1608Metric; LCSC C25804
R72: 49.9; R_0603_1608Metric
U15: TPS62933; SOT-583-8

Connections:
+5V: C55.1, C56.1, C57.1, L1.2, R11.1, R72.2; also elsewhere on the board
GND: C6.2, C24.2, C52.2, C53.2, C55.2, C56.2, C57.2, D8.1 (K), R67.2, R70.1, U15.4 (GND); also elsewhere on the board
unnamed: C54.2, R68.2
unnamed: C58.1, R69.2, R72.1
unnamed: D8.2 (A), R11.2
unnamed: JP5.1 (A), U15.1 (RT)
unnamed: JP5.2 (B), R67.1
unnamed: R68.1, U15.6 (BST)
unnamed: C58.2, R69.1, R70.2, U15.8 (FB)
unnamed: C53.1, U15.7 (SS)
unnamed: C54.1, L1.1, U15.5 (SW)
main: C6.1, C24.1, C52.1, U15.3 (VIN); also elsewhere on the board

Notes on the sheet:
Enable input to the converter. Driving EN high or leaving this pin floating enable the converter. (Datasheet page 3)
RT controls the switching frequency floating: 500kHz GND: 1200kHz RT to GND: 8.9k to 11k: 200kHz to 2200 kHz (Datasheet p. 20)
@todo: use high quality capacitors with sufficient voltage rating
Datasheet 9.3.4 Setting RFBB = 10 kΩ and RFBT in the range of 10 kΩ to 300 kΩ is recommended for most applications.

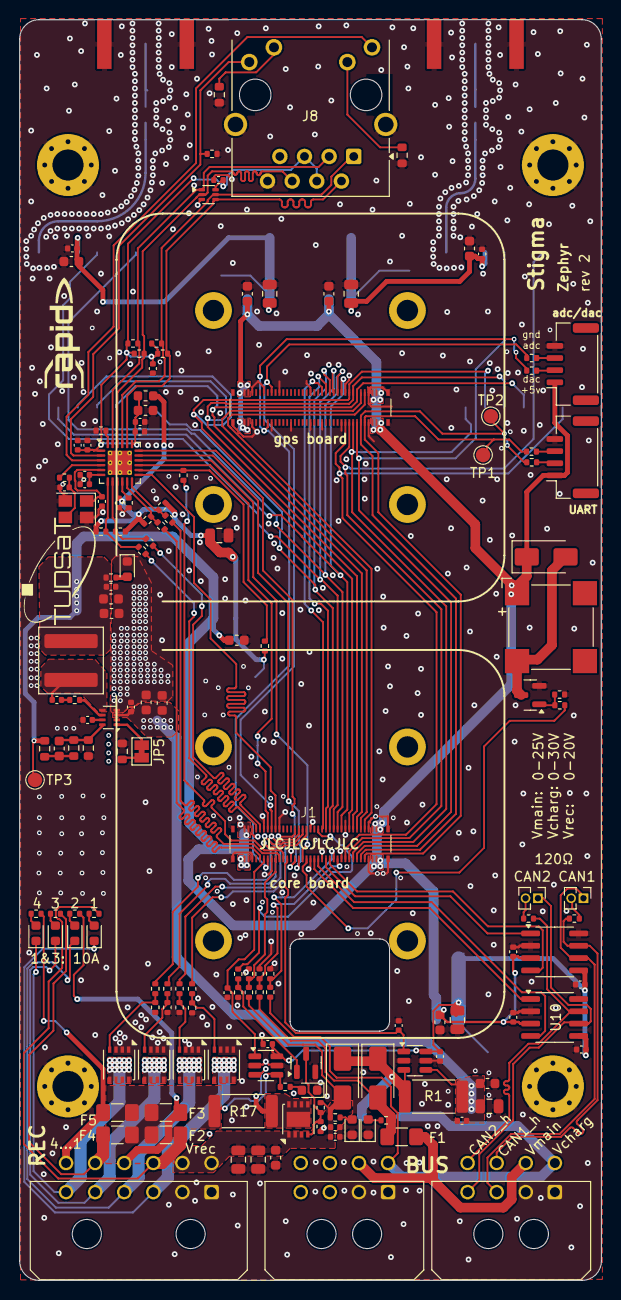
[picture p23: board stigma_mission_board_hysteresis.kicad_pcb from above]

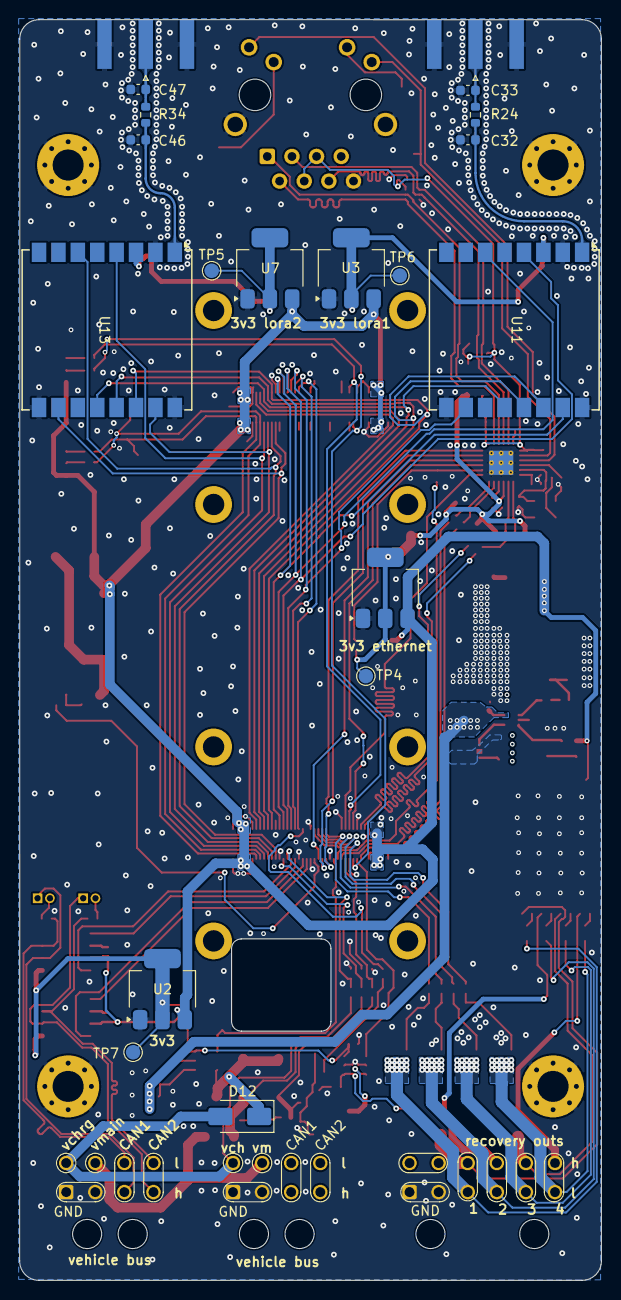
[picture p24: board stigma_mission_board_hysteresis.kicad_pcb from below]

Board: 4 copper layers, 60.0 x 130.0 mm, 181 parts (19 on the bottom side), 124 nets.

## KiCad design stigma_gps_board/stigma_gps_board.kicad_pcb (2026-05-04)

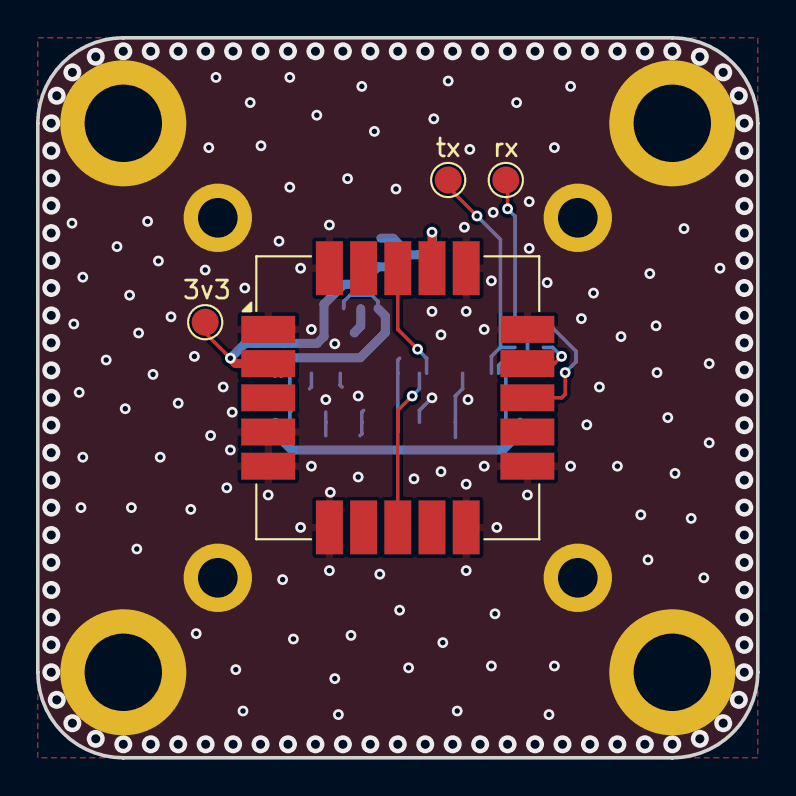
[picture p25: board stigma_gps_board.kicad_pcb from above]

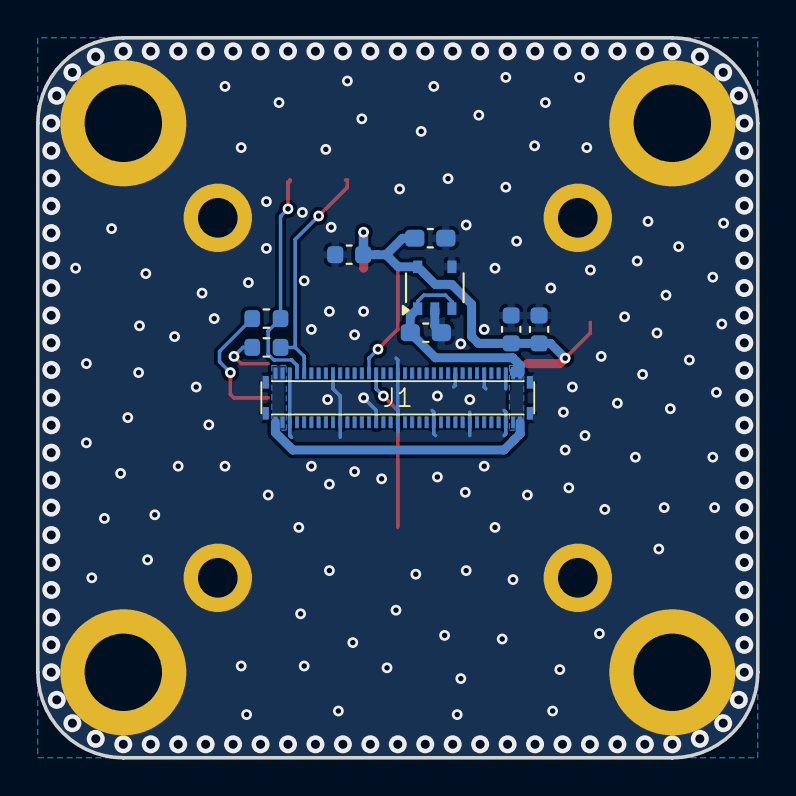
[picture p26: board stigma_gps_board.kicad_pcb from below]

Board: 2 copper layers, 40.0 x 40.0 mm, 21 parts (9 on the bottom side), 9 nets.

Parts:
C1, C2: 1uF; C_0603_1608Metric_Pad1.08x0.95mm_HandSolder
C3, C4, C5: 100n; C_0603_1608Metric
H1, H2, H3, H4: MountingHole_Pad; MountingHole_2.2mm_M2_ISO14580_Pad
H5, H6, H7, H8: MountingHole_Pad; MountingHole_4.3mm_M4_ISO14580_Pad
J1: DF40GB-70DP-0.4V; DF40GB-70DP-0.4V-plug
L1, L2: BEAD; L_0603_1608Metric
TP1: tx; TestPoint_Pad_D1.5mm
TP2: rx; TestPoint_Pad_D1.5mm
TP3: 3v3; TestPoint_Pad_D1.5mm
U1: NCP115AMX120TCG; TSOP-5_1.65x3.05mm_P0.95mm
U2: SAM-M10Q; ublox_SAM-M8Q_HandSolder

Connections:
+3.3V: C2.2, C3.2, C4.2, C5.2, TP3.1, U1.5 (OUT), U2.2 (VCC_IO), U2.17 (VCC)
+5V: C1.2, J1.1, J1.2, J1.34, J1.35, J1.36, J1.37, J1.69, J1.70, U1.1 (IN), U1.3 (EN)
GND: C1.1, C2.1, C3.1, C4.1, C5.1, H1.1, H2.1, H3.1, H4.1, H5.1, H6.1, H7.1, H8.1, J1.3, J1.9, J1.18, J1.26, J1.30, J1.33, J1.38, J1.45, J1.50, J1.53, J1.58, J1.63, J1.68, J1.SH (Shield), U1.2 (GND), U1.4 (NC), U2.1 (GND), U2.4 (GND), U2.5 (GND), U2.6 (GND), U2.10 (GND), U2.11 (GND), U2.15 (GND), U2.16 (GND), U2.20 (GND)
GPS_RESET: J1.14, U2.18 (~RESET)
GPS_SAFEBOOT: J1.15, U2.8 (~SAFEBOOT)
unnamed: L1.1, U2.14 (RXD)
unnamed: L2.1, U2.13 (TXD)
UART8_RX_GPS: J1.4, L2.2, TP2.1
UART8_TX_GPS: J1.5, L1.2, TP1.1

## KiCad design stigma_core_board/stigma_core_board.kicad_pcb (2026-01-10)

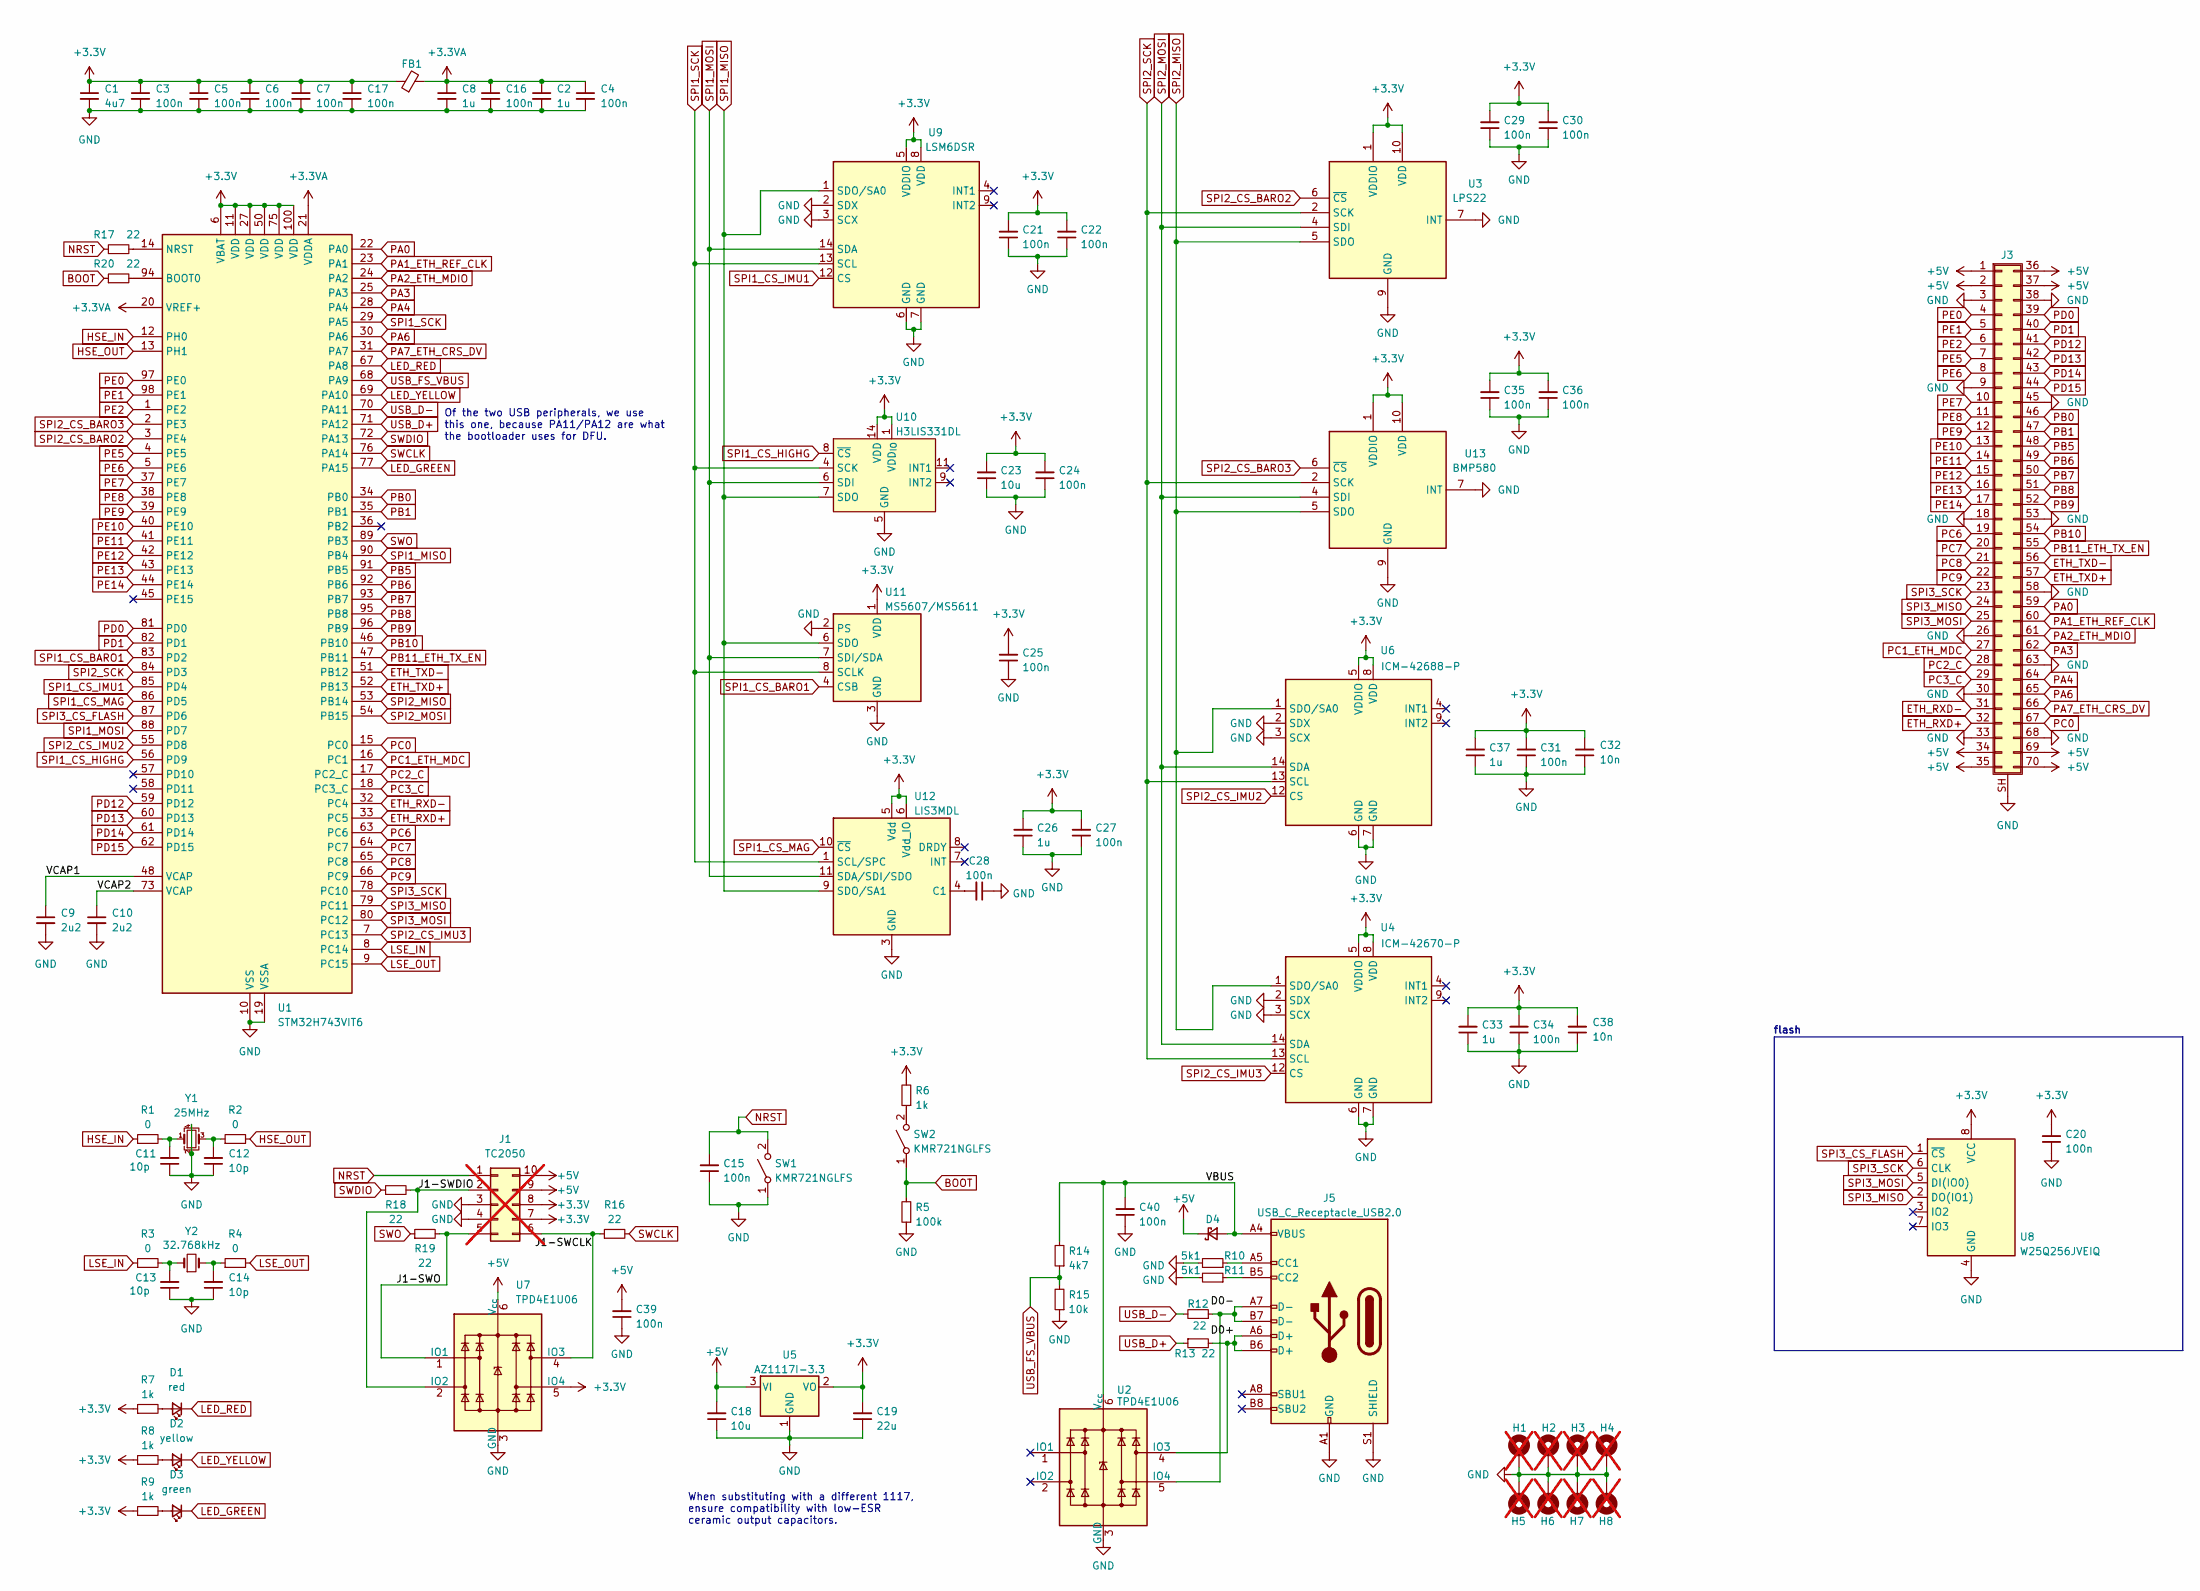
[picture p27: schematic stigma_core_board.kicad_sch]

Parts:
C1: 4u7; C_0603_1608Metric; LCSC C19666
C2, C8: 1u; C_0402_1005Metric; LCSC C52923
C3, C4, C5, C6, C7, C16, C17: 100n; C_0402_1005Metric; LCSC C1525
C9, C10: 2u2; C_0402_1005Metric; LCSC C12530
C11, C12, C13, C14: 10p; C_0402_1005Metric; LCSC C32949
C15, C20, C21, C22, C24, C25, C27, C28, C29, C30, C31, C34, C35, C36, C39, C40: 100n; C_0402_1005Metric; Part# CL10B104KB8NNNC; LCSC C1525
C18, C23: 10u; C_0603_1608Metric; Part# CL31B106KAHNNNE; LCSC C19702
C19: 22u; C_0603_1608Metric; Part# CL31A226KAHNNNE; LCSC C86295
C26, C33, C37: 1u; C_0402_1005Metric; Part# CL21A105KBCLNNC; LCSC C52923
C32, C38: 10n; C_0402_1005Metric; Part# CL10B104KB8NNNC; LCSC C15195
D1: red; LED_0603_1608Metric; LCSC C2286
D2: yellow; LED_0603_1608Metric; LCSC C72038
D3: green; LED_0603_1608Metric; LCSC C965804
D4: D_SOD-123; Part# PMEG3020EH,115; LCSC C8598
FB1: FerriteBead_Small; R_0603_1608Metric; LCSC C1002
H1, H2, H3, H4: MountingHole_Pad; MountingHole_4.3mm_M4_ISO14580_Pad; not fitted
H5, H6, H7, H8: MountingHole_Pad; MountingHole_2.2mm_M2_ISO14580_Pad; not fitted
J1: TC2050; Tag-Connect_TC2050-IDC-FP_2x05_P1.27mm_Vertical; not fitted
J3: CONN PLUG 70POS SMD GOLD; DF40GB-70DP-0.4V-plug; LCSC# C2692097
J5: USB_C_Receptacle_USB2.0; USB_C_Receptacle_Palconn_UTC16-G; Part# KH-TYPE-C-16P; LCSC C709357
R1, R2, R3, R4: 0; R_0402_1005Metric; LCSC C17168
R5: 100k; R_0402_1005Metric; Part# RC0603FR-0710KL; LCSC C25741
R6: 1k; R_0402_1005Metric; Part# RC0603FR-0710KL; LCSC C11702
R7, R8, R9: 1k; R_0402_1005Metric; LCSC C11702
R10, R11: 5k1; R_0402_1005Metric; Part# RC0603FR-075K1L; LCSC C25905
R12, R13: 22; R_0402_1005Metric; Part# RC0603FR-0722RL; LCSC C25092
R14: 4k7; R_0402_1005Metric; Part# RC0603FR-0710KL; LCSC C25900
R15: 10k; R_0402_1005Metric; Part# RC0603FR-0710KL; LCSC C25744
R16, R17, R18, R19, R20: 22; R_0402_1005Metric; Part# RC0603FR-0710KL; LCSC C25092
SW1, SW2: KMR721NGLFS; SW_Push_1P1T_NO_CK_KMR2; Part# KMR721NGLFS; LCSC C2911418
U1: STM32H743VIT6; LQFP-100_14x14mm_P0.5mm; LCSC C114409
U2, U7: TPD4E1U06; SOT-563; LCSC C527516
U3: LPS22; ST_HLGA-10_2x2mm_P0.5mm_LayoutBorder3x2y; LCSC C2827824
U4: ICM-42670-P; LGA-14_3x2.5mm_P0.5mm_LayoutBorder3x4y; LCSC C3288646
U5: AZ1117I-3.3; SOT-223-3_TabPin2; Part# AZ1117CH-3.3TRG1; LCSC C92102
U6: ICM-42688-P; LGA-14_3x2.5mm_P0.5mm_LayoutBorder3x4y; Part# LSM6DSRTR; LCSC C1850418
U8: W25Q256JVEIQ; WSON-8-1EP_8x6mm_P1.27mm_EP3.4x4.3mm; LCSC C97522
U9: LSM6DSR; LGA-14_3x2.5mm_P0.5mm_LayoutBorder3x4y; Part# LSM6DSRTR; LCSC C784817
U10: H3LIS331DL; LGA-16_3x3mm_P0.5mm_LayoutBorder3x5y; Part# H3LIS331DLTR; DigiKey# 497-13903-1-ND
U11: MS5607/MS5611; LGA-8_3x5mm_P1.25mm; Part# MS561101BA03-50; DigiKey# 223-1622-1-ND
U12: LIS3MDL; LGA-12_2x2mm_P0.5mm; Part# LIS3MDLTR; DigiKey# 497-13892-1-ND
U13: BMP580; ST_HLGA-10_2x2mm_P0.5mm_LayoutBorder3x2y; LCSC C22391138
Y1: 25MHz; Crystal_SMD_3225-4Pin_3.2x2.5mm; LCSC C9006
Y2: 32.768kHz; Crystal_SMD_3215-2Pin_3.2x1.5mm; LCSC C70509

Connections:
+3.3V: C1.1, C3.1, C5.1, C6.1, C7.1, C17.1, C19.2, C20.2, C21.2, C22.2, C23.2, C24.2, C25.2, C26.2, C27.2, C29.2, C30.2, C31.2, C32.2, C33.2, C34.2, C35.2, C36.2, C37.2, C38.2, FB1.1, J1.7, J1.8, R6.2, R7.1, R8.1, R9.1, U1.6 (VBAT), U1.11 (VDD), U1.27 (VDD), U1.50 (VDD), U1.75 (VDD), U1.100 (VDD), U3.1 (VDDIO), U3.10 (VDD), U4.5 (VDDIO), U4.8 (VDD), U5.2 (VO), U6.5 (VDDIO), U6.8 (VDD), U7.5 (IO4), U8.8 (VCC), U9.5 (VDDIO), U9.8 (VDD), U10.1 (VDD_{IO}), U10.14 (VDD), U10.15 (reserved), U11.1 (VDD), U12.5 (Vdd), U12.6 (Vdd_IO), U13.1 (VDDIO), U13.10 (VDD)
+3.3VA: C2.1, C4.1, C8.1, C16.1, FB1.2, U1.20 (VREF+), U1.21 (VDDA)
+5V: C18.2, C39.2, D4.1 (K), J1.9, J1.10, J3.1, J3.2, J3.34, J3.35, J3.36, J3.37, J3.69, J3.70, U5.3 (VI), U7.6 (V_{cc})
/D0+: J5.A6 (D+), J5.B6 (D+), R13.2, U2.4 (IO3)
/D0-: J5.A7 (D-), J5.B7 (D-), R12.1, U2.5 (IO4)
/J1-SWDIO: J1.2, R18.2, U7.2 (IO2)
/J1-SWO: J1.5, R19.2, U7.1 (IO1)
/VBUS: C40.2, D4.2 (A), J5.A4 (VBUS), J5.A9 (VBUS), J5.B4 (VBUS), J5.B9 (VBUS), R14.2, U2.6 (V_{cc})
/VCAP1: C9.1, U1.48 (VCAP)
/VCAP2: C10.1, U1.73 (VCAP)
BOOT: R5.2, R20.1, SW2.1 (A)
ETH_RXD+: J3.32, U1.33 (PC5)
ETH_RXD-: J3.31, U1.32 (PC4)
ETH_TXD+: J3.57, U1.52 (PB13)
ETH_TXD-: J3.56, U1.51 (PB12)
GND: C1.2, C2.2, C3.2, C4.2, C5.2, C6.2, C7.2, C8.2, C9.2, C10.2, C11.1, C12.1, C13.1, C14.1, C15.1, C16.2, C17.2, C18.1, C19.1, C20.1, C21.1, C22.1, C23.1, C24.1, C25.1, C26.1, C27.1, C28.1, C29.1, C30.1, C31.1, C32.1, C33.1, C34.1, C35.1, C36.1, C37.1, C38.1, C39.1, C40.1, H1.1, H2.1, H3.1, H4.1, H5.1, H6.1, H7.1, H8.1, J1.3, J1.4, J3.3, J3.9, J3.18, J3.26, J3.30, J3.33, J3.38, J3.45, J3.53, J3.58, J3.63, J3.68, J3.SH (Shield), J5.A1 (GND), J5.A12 (GND), J5.B1 (GND), J5.B12 (GND), J5.S1 (SHIELD), R5.1, R10.2, R11.2, R15.1, SW1.1 (A), U1.10 (VSS), U1.19 (VSSA), U1.26 (VSS), U1.49 (VSS), U1.74 (VSS), U1.99 (VSS), U2.3 (GND), U3.3 (GND), U3.7 (INT), U3.8 (GND), U3.9 (GND), U4.2 (SDX), U4.3 (SCX), U4.6 (GND), U4.7 (GND), U5.1 (GND), U6.2 (SDX), U6.3 (SCX), U6.6 (GND), U6.7 (GND), U7.3 (GND), U8.4 (GND), U9.2 (SDX), U9.3 (SCX), U9.6 (GND), U9.7 (GND), U10.5 (GND), U10.10 (reserved), U10.12 (GND), U10.13 (GND), U10.16 (GND), U11.2 (PS), U11.3 (GND), U12.2 (GND), U12.3 (GND), U12.12 (GND), U13.3 (GND), U13.7 (INT), U13.8 (GND), U13.9 (GND), Y1.2, Y1.4
HSE_IN: R1.1, U1.12 (PH0)
HSE_OUT: R2.2, U1.13 (PH1)
LED_GREEN: D3.1 (K), U1.77 (PA15)
LED_RED: D1.1 (K), U1.67 (PA8)
LED_YELLOW: D2.1 (K), U1.69 (PA10)
LSE_IN: R3.1, U1.8 (PC14)
LSE_OUT: R4.2, U1.9 (PC15)
NRST: C15.2, J1.1, R17.1, SW1.2 (B)
unnamed: C11.2, R1.2, Y1.1
unnamed: C12.2, R2.1, Y1.3
unnamed: C13.2, R3.2, Y2.1
unnamed: C14.2, R4.1, Y2.2
unnamed: D1.2 (A), R7.2
unnamed: D2.2 (A), R8.2
unnamed: D3.2 (A), R9.2
unnamed: J1.6, R16.1, U7.4 (IO3)
unnamed: J5.A5 (CC1), R10.1
unnamed: J5.B5 (CC2), R11.1
unnamed: R6.1, SW2.2 (B)
unnamed: R20.2, U1.94 (BOOT0)
unnamed: R17.2, U1.14 (NRST)
unnamed: C28.2, U12.4 (C1)
PA0: J3.59, U1.22 (PA0)
PA1_ETH_REF_CLK: J3.60, U1.23 (PA1)
PA2_ETH_MDIO: J3.61, U1.24 (PA2)
PA3: J3.62, U1.25 (PA3)
PA4: J3.64, U1.28 (PA4)
PA6: J3.65, U1.30 (PA6)
PA7_ETH_CRS_DV: J3.66, U1.31 (PA7)
PB0: J3.46, U1.34 (PB0)
PB1: J3.47, U1.35 (PB1)
PB5: J3.48, U1.91 (PB5)
PB6: J3.49, U1.92 (PB6)
PB7: J3.50, U1.93 (PB7)
PB8: J3.51, U1.95 (PB8)
PB9: J3.52, U1.96 (PB9)
PB10: J3.54, U1.46 (PB10)
PB11_ETH_TX_EN: J3.55, U1.47 (PB11)
PC0: J3.67, U1.15 (PC0)
PC1_ETH_MDC: J3.27, U1.16 (PC1)
PC2_C: J3.28, U1.17 (PC2_C)
PC3_C: J3.29, U1.18 (PC3_C)
PC6: J3.19, U1.63 (PC6)
PC7: J3.20, U1.64 (PC7)
PC8: J3.21, U1.65 (PC8)
PC9: J3.22, U1.66 (PC9)
PD0: J3.39, U1.81 (PD0)
PD1: J3.40, U1.82 (PD1)
PD12: J3.41, U1.59 (PD12)
PD13: J3.42, U1.60 (PD13)
PD14: J3.43, U1.61 (PD14)
PD15: J3.44, U1.62 (PD15)
PE0: J3.4, U1.97 (PE0)
PE1: J3.5, U1.98 (PE1)
PE2: J3.6, U1.1 (PE2)
PE5: J3.7, U1.4 (PE5)
PE6: J3.8, U1.5 (PE6)
PE7: J3.10, U1.37 (PE7)
PE8: J3.11, U1.38 (PE8)
PE9: J3.12, U1.39 (PE9)
PE10: J3.13, U1.40 (PE10)
PE11: J3.14, U1.41 (PE11)
PE12: J3.15, U1.42 (PE12)
PE13: J3.16, U1.43 (PE13)
PE14: J3.17, U1.44 (PE14)
SPI1_CS_BARO1: U1.83 (PD2), U11.4 (CSB), U11.5 (CSB)
SPI1_CS_HIGHG: U1.56 (PD9), U10.8 (~CS)
SPI1_CS_IMU1: U1.85 (PD4), U9.12 (CS)
SPI1_CS_MAG: U1.86 (PD5), U12.10 (~CS)
SPI1_MISO: U1.90 (PB4), U9.1 (SDO/SA0), U10.7 (SDO), U11.6 (SDO), U12.9 (SDO/SA1)
SPI1_MOSI: U1.88 (PD7), U9.14 (SDA), U10.6 (SDI), U11.7 (SDI/SDA), U12.11 (SDA/SDI/SDO)
SPI1_SCK: U1.29 (PA5), U9.13 (SCL), U10.4 (SCK), U11.8 (SCLK), U12.1 (SCL/SPC)
SPI2_CS_BARO2: U1.3 (PE4), U3.6 (~CS)
SPI2_CS_BARO3: U1.2 (PE3), U13.6 (~CS)
SPI2_CS_IMU2: U1.55 (PD8), U6.12 (CS)
SPI2_CS_IMU3: U1.7 (PC13), U4.12 (CS)
SPI2_MISO: U1.53 (PB14), U3.5 (SDO), U4.1 (SDO/SA0), U6.1 (SDO/SA0), U13.5 (SDO)
SPI2_MOSI: U1.54 (PB15), U3.4 (SDI), U4.14 (SDA), U6.14 (SDA), U13.4 (SDI)
SPI2_SCK: U1.84 (PD3), U3.2 (SCK), U4.13 (SCL), U6.13 (SCL), U13.2 (SCK)
SPI3_CS_FLASH: U1.87 (PD6), U8.1 (~CS)
SPI3_MISO: J3.24, U1.79 (PC11), U8.2 (DO(IO1))
SPI3_MOSI: J3.25, U1.80 (PC12), U8.5 (DI(IO0))
SPI3_SCK: J3.23, U1.78 (PC10), U8.6 (CLK)
SWCLK: R16.2, U1.76 (PA14)
SWDIO: R18.1, U1.72 (PA13)
SWO: R19.1, U1.89 (PB3)
USB_D+: R13.1, U1.71 (PA12)
USB_D-: R12.2, U1.70 (PA11)
USB_FS_VBUS: R14.1, R15.2, U1.68 (PA9)

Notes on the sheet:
Of the two USB peripherals, we use this one, because PA11/PA12 are what the bootloader uses for DFU.
flash
When substituting with a different 1117, ensure compatibility with low-ESR ceramic output capacitors.

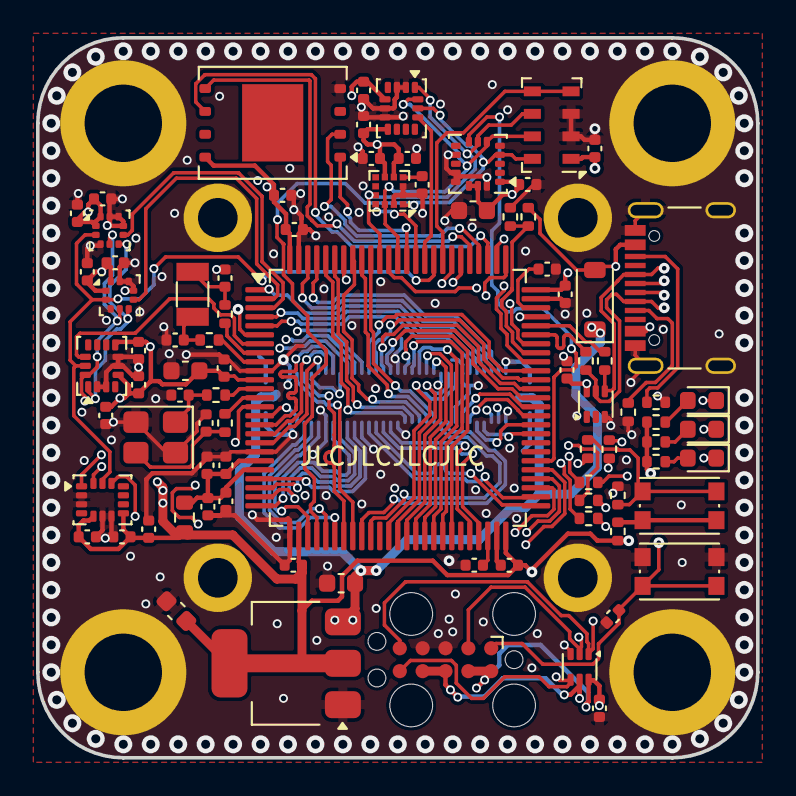
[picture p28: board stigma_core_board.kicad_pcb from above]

Board: 4 copper layers, 40.0 x 40.0 mm, 93 parts (1 on the bottom side), 105 nets.

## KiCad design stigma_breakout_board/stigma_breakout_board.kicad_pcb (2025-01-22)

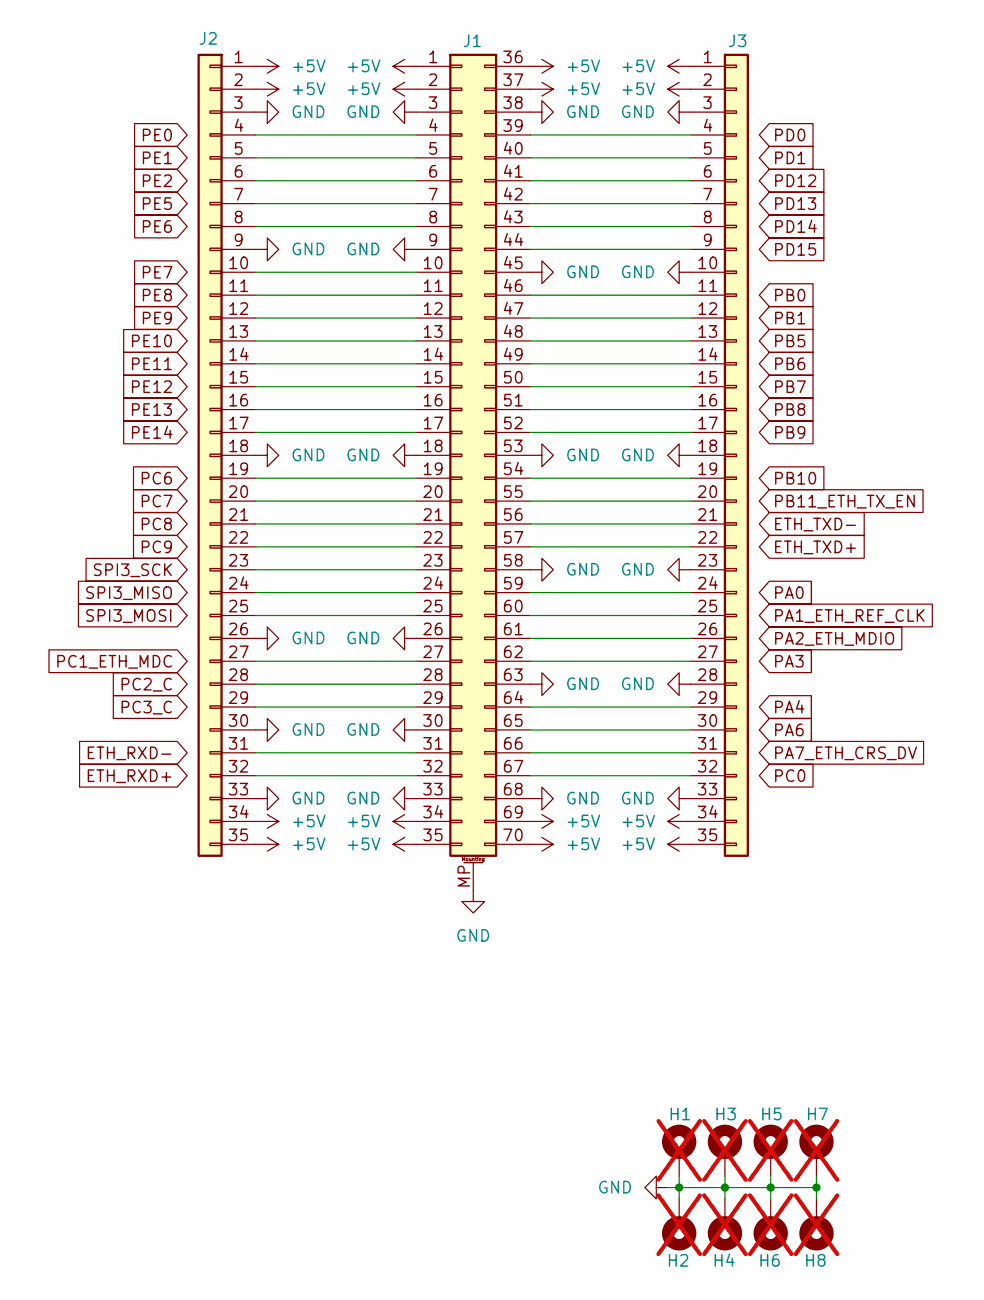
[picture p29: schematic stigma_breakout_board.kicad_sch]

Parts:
H1, H3, H5, H7: MountingHole_Pad; MountingHole_4.3mm_M4_ISO14580_Pad; not fitted
H2, H4, H6, H8: MountingHole_Pad; MountingHole_2.2mm_M2_ISO14580_Pad; not fitted
J1: DF40C-70DS-0.4V-receptacle
J2, J3: Conn_01x35; PinHeader_1x35_P2.54mm_Vertical

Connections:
+5V: J1.1, J1.2, J1.34, J1.35, J1.36, J1.37, J1.69, J1.70, J2.1, J2.2, J2.34, J2.35, J3.1, J3.2, J3.34, J3.35
GND: H1.1, H2.1, H3.1, H4.1, H5.1, H6.1, H7.1, H8.1, J1.3, J1.9, J1.18, J1.26, J1.30, J1.33, J1.38, J1.45, J1.53, J1.58, J1.63, J1.68, J1.MP (MountPin), J2.3, J2.9, J2.18, J2.26, J2.30, J2.33, J3.3, J3.10, J3.18, J3.23, J3.28, J3.33
unnamed: J1.4, J2.4
unnamed: J1.5, J2.5
unnamed: J1.6, J2.6
unnamed: J1.7, J2.7
unnamed: J1.8, J2.8
unnamed: J1.10, J2.10
unnamed: J1.11, J2.11
unnamed: J1.12, J2.12
unnamed: J1.13, J2.13
unnamed: J1.14, J2.14
unnamed: J1.15, J2.15
unnamed: J1.16, J2.16
unnamed: J1.17, J2.17
unnamed: J1.19, J2.19
unnamed: J1.20, J2.20
unnamed: J1.21, J2.21
unnamed: J1.22, J2.22
unnamed: J1.23, J2.23
unnamed: J1.24, J2.24
unnamed: J1.25, J2.25
unnamed: J1.27, J2.27
unnamed: J1.28, J2.28
unnamed: J1.29, J2.29
unnamed: J1.31, J2.31
unnamed: J1.32, J2.32
unnamed: J1.39, J3.4
unnamed: J1.40, J3.5
unnamed: J1.41, J3.6
unnamed: J1.42, J3.7
unnamed: J1.43, J3.8
unnamed: J1.44, J3.9
unnamed: J1.46, J3.11
unnamed: J1.47, J3.12
unnamed: J1.48, J3.13
unnamed: J1.49, J3.14
unnamed: J1.50, J3.15
unnamed: J1.51, J3.16
unnamed: J1.52, J3.17
unnamed: J1.54, J3.19
unnamed: J1.55, J3.20
unnamed: J1.56, J3.21
unnamed: J1.57, J3.22
unnamed: J1.59, J3.24
unnamed: J1.60, J3.25
unnamed: J1.61, J3.26
unnamed: J1.62, J3.27
unnamed: J1.64, J3.29
unnamed: J1.65, J3.30
unnamed: J1.66, J3.31
unnamed: J1.67, J3.32

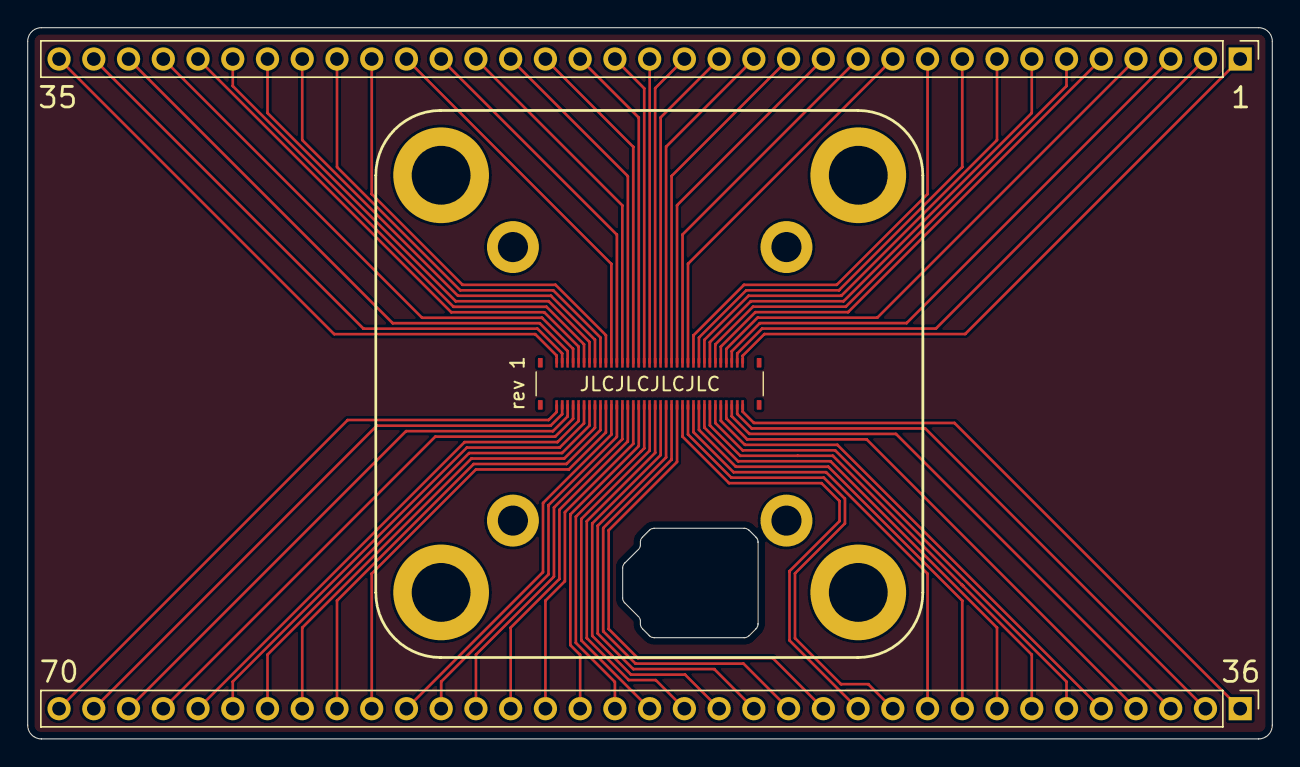
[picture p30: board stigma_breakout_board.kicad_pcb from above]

Board: 2 copper layers, 91.0 x 52.0 mm, 11 parts (0 on the bottom side), 52 nets.

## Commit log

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2024-12-16 initialized gps board with first parts and infos in the scematic
    [stigma_gps_board.kicad_pcb, stigma_gps_board.kicad_sch]
2024-12-19 added esd protection, finished scematic
    [stigma_gps_board.kicad_pcb, stigma_gps_board.kicad_sch]
2024-12-20 Clean up previous pinout attempt
    [stigma_core_board.kicad_sch]
2024-12-20 first revision of gps board finished
    [DF40GB-10DP-0.4V.igs, SAM-M8Q-0.stp, stigma_gps_board.kicad_pcb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]
2024-12-20 added stm32 and connector pinout
    [stigma_core_board.kicad_sch]
2025-01-13 add connector and fix recovery
    [stigma_mission_board_hysteresis.kicad_sch]
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2025-01-22 First pass of signal routing
    [stigma_core_board.kicad_pcb, stigma_core_board.kicad_sch]
2025-01-22 Route power, please DRC
    [stigma_core_board.kicad_pcb, stigma_core_board.kicad_sch]
2025-01-22 Rename LCSC part no. property
    [stigma_core_board.kicad_pcb, stigma_core_board.kicad_sch]
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2025-01-22 Minor routing tweaks, add net colors
    [stigma_core_board.kicad_pcb, stigma_core_board.kicad_sch]
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2025-01-22 Add correct load capacitors, tweak USB routing, fab options
    [stigma_core_board.kicad_pcb, stigma_core_board.kicad_sch]
2025-01-22 Add first draft of breakout board
    [stigma_breakout_board.kicad_pcb, stigma_breakout_board.kicad_sch]
2025-01-22 Move GPS project to root folder
    [stigma_gps_board.kicad_pcb, stigma_gps_board.kicad_sch]
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2025-01-27 added second lora module, adapted connector pins
    [stigma_mission_board_hysteresis.kicad_sch, untitled.kicad_sch]
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2025-01-29 fix ethernet, add VH bus, fix voltage sensing
    [recovery_output.kicad_sch, stigma_mission_board_hysteresis.kicad_sch]
2025-01-30 improve pinout and add more descriptions
    [stigma_mission_board_hysteresis.kicad_sch]
2025-02-01 fixed a few small issues, added some part numbers and footprints
    [recovery_output.kicad_sch, stigma_mission_board_hysteresis.kicad_sch]
2025-02-01 changed mosfet to more suitable one
    [recovery_output.kicad_sch]
2025-02-01 changed vehicle bus connector numbering
    [recovery_output.kicad_sch, stigma_mission_board_hysteresis.kicad_sch]
2025-02-04 add high_voltage to pwm signal again
    [recovery_output.kicad_sch]
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2025-02-07 some changes to the recovery outputs
    [recovery_output.kicad_sch, stigma_mission_board_hysteresis.kicad_sch]
2025-02-09 uploaded files to share current not working parts
    [recovery_output.kicad_sch, stigma_core_board.kicad_pcb, stigma_core_board.kicad_sch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]
2025-02-11 Added missing footprints and changed GPS Connector
    [recovery_output.kicad_sch, stigma_mission_board_hysteresis.kicad_pcb, stigma_mission_board_hysteresis.kicad_sch]
2025-02-11 Added missing Footprints and changed GPS Connector
    into the right directory this time
    [recovery_output.kicad_sch, stigma_mission_board_hysteresis.kicad_pcb, stigma_mission_board_hysteresis.kicad_sch]
2025-02-11 fixed some errors
    [recovery_output.kicad_sch, stigma_mission_board_hysteresis.kicad_sch]
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2025-02-24 changed pcb layout and added first tracks
    [stigma_mission_board_hysteresis.kicad_pcb]
2025-02-26 placed recovery outputs and vehicle bus, fixed errors in schematic
    [recovery_output.kicad_sch, stigma_mission_board_hysteresis.kicad_pcb, stigma_mission_board_hysteresis.kicad_sch]
2025-02-28 made board more compact, started routing recovery outputs
    [recovery_output.kicad_sch, stigma_mission_board_hysteresis.kicad_pcb, stigma_mission_board_hysteresis.kicad_sch]
2025-02-28 some tydiing up and adding footprints
    [recovery_output.kicad_sch, stigma_mission_board_hysteresis.kicad_pcb, stigma_mission_board_hysteresis.kicad_sch]
2025-02-28 added the other 2 recovery outputs and sorted all components
    [recovery_output.kicad_sch, stigma_mission_board_hysteresis.kicad_pcb, stigma_mission_board_hysteresis.kicad_sch]
2025-03-02 Restore stigma_core_board from 4524638
    [stigma_core_board.kicad_pcb, stigma_core_board.kicad_sch]
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2025-03-03 added GPS and Coreboard connector, changed ROs
    [stigma_mission_board_hysteresis.kicad_pcb, stigma_mission_board_hysteresis.kicad_sch]
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2025-03-21 added 3d models of connectors
    [df40c-70ds-0_4v_51_.stp, df40hb_2_5_-10ds-0_4v_51_.stp, recovery_output.kicad_sch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]
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2025-03-24 fixed footprint
2025-03-24 changed pcb design. currently not working
    [recovery_output.kicad_sch, stigma_mission_board_hysteresis.kicad_pcb, stigma_mission_board_hysteresis.kicad_sch]
2025-03-24 Layed out 3.3v regulators, buzzer, shift register and current + voltage sensing on the mission board pcb
    [stigma_mission_board_hysteresis.kicad_pcb, stigma_mission_board_hysteresis.kicad_sch]
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2025-03-26 added 5v regulators to pcb
    [stigma_mission_board_hysteresis.kicad_pcb]
2025-03-29 added ethernet layout to pcb and changed minor errors
    [stigma_mission_board_hysteresis.kicad_pcb, stigma_mission_board_hysteresis.kicad_sch]
2025-04-03 Temp save of changes. Changed PCB size, layout and number of Connectors
    [stigma_mission_board_hysteresis.kicad_pcb]
2025-04-03 Added more components to NEW pcb layout.
    [recovery_output.kicad_sch, stigma_mission_board_hysteresis.kicad_pcb, stigma_mission_board_hysteresis.kicad_sch]
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2025-04-06 added some 3d models
    [ANT-TH_L14.8-W6.4-H10.0.step, RJ45-TH_MJ88B-B011-RVL11-P.step, recovery_output.kicad_sch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]
2025-04-07 added 3d models and datasheets
    [BUZ-SMD_4P-L8.5-W8.5-H3.0.step, COMM-SMD_L17.0-W16.0-H3.2-RA-01S (1).step, stigma_core_board.step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]
2025-04-18 Rework recovery outputs to 2x2 low side
    [recovery_output.kicad_sch, stigma_mission_board_hysteresis.kicad_pcb, stigma_mission_board_hysteresis.kicad_sch]
2025-04-19 Refactor schematic, esp. recovery outputs, prepare for final layout
    [recovery_output.kicad_sch, stigma_mission_board_hysteresis.kicad_pcb, stigma_mission_board_hysteresis.kicad_sch]
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2025-04-22 progress on routing, add some 3d models
    [66200821022.stp, 66201021022.stp, 66201221022.stp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]
2025-04-27 progress on mission board layout
    [recovery_output_pair.kicad_sch, stigma_mission_board_hysteresis.kicad_pcb, stigma_mission_board_hysteresis.kicad_sch]
2025-05-09 Complete routing of mission board
    [recovery_output_pair.kicad_sch, stigma_mission_board_hysteresis.kicad_pcb, stigma_mission_board_hysteresis.kicad_sch]
2025-05-12 Last minute changes to mission board
    [recovery_output_pair.kicad_sch, stigma_mission_board_hysteresis.kicad_pcb, stigma_mission_board_hysteresis.kicad_sch]
2025-06-15 Update GPS board for mission board
    [stigma_gps_board.kicad_pcb, stigma_gps_board.kicad_sch]
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2025-10-17 remove rst and boot from USB TSV diode
    [stigma_core_board.kicad_pcb, stigma_core_board.kicad_sch]
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2025-11-09 replace voltage regulator and increase edge-cut corner radius to match the core board
    [recovery_output_pair.kicad_sch, stigma_mission_board_hysteresis.kicad_pcb, stigma_mission_board_hysteresis.kicad_sch]
2025-12-01 fix voltage regulator
    [recovery_output_pair.kicad_sch, stigma_gps_board.kicad_pcb, stigma_gps_board.kicad_sch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]
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2026-01-10 core: Replace flash w/ W25Q256, WSON 8x6
    [stigma_core_board.kicad_pcb, stigma_core_board.kicad_sch]
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2026-02-16 improve can traces at VB, use smaller resistor for voltage reg.
    [stigma_mission_board_hysteresis.kicad_pcb, stigma_mission_board_hysteresis.kicad_sch, voltage_regulator.kicad_sch]
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2026-03-23 design check finished, some cosmetic changes, part adaptions, prints, etc.
    [recovery_output_pair.kicad_sch, stigma_mission_board_hysteresis.kicad_pcb, stigma_mission_board_hysteresis.kicad_sch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]
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
